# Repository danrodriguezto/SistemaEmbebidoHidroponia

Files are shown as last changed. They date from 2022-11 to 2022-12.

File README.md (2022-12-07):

# **Sistema Embebido para control de cultivo por hidroponia.** #

----
#### Daniel Esteban Rodriguez ####

#### Daniel Santiago Robayo ####

#### María Camila Muñoz Berrio ####

#### Sebastian Ruiz Torres ####

----
## **Descripción del problema** ## 

En la actualidad obtener alimentos vegetales con los nutrientes necesario y sin tanto procesamiento quimico a un valor moderado no es sencillo por lo que la idea de cultivar autonomamente los alimentos en una huerta casera se hace una mejor opción. Ahora, cultivar en la ciudad trae multiples desafios como los son el espacio, el tiempo que es posible dedicarle a esta labor y la falta de conocimiento en esto. De alli nacen vaias alternativas que pretenden reeemplazar las huertas en suelo convencionales por formas más eficientes de cutivar en el mismo espacio y por un valor menor.

Las principales alternativas son: Acuaponía, aeroponía e hidroponía. Esta ultima fue la elegida para desarrollar el proyecto debido a que esta se desarrolla en el agua, esto quiere decir que la raíz se desarrolla en un sustrato o en la misma solución liquida nutritiva utilizada.

## **Propuesta** ##
Se plantea construir un cultivo vertical de hidroponia que reduzca el espacio utilizado para un cultivo y que cuente con un sistema de monitoreo que cuente con sensores previamente calibrados que midan variables importantes para el sostenimiento del cultivo, estos sensores enviaran información que sera procesada y a partir de esto se enviaran alertas al telefono movil del usuario haciendo así interactivo el proceso de producir su alimento. También se pretende que esta dispositivo pueda ser usado por cualquier persona incluso si no conoce sobre hidroponia por medio de avisos informativos-educativos. 

**Publico objetivo** Personas con interesadas en cultivar en espacios reducidos sin la necesidad de dañar los suelos y aprender sobre cultivos hidroponicos.

**Objetivo General**  Diseño, creacion y aplicacion  de un sistema de monitoreo que permita la optimizacion del cultivo y la interaccion educativa con el usuario.

unknown

----
## **Requerimientos** ##
* Medir la temperatura de agua
* Medir el nivel del agua
* Ser ergonomico
* Recirculamiento del agua eficiente

## **Diagrama de bloques del sistema.** ##

En el siguiente diagrama se muestran los diferentes componentes que se plantean implementar en el sistema, en este se pueden observar cada una de las entradas y salidas que se pretenden tener en el sistema. Como interacción principal con el usuario se va a construir un sistema que conecte con el telefono del usuario y lo alerte sobre las condiciones de la planta.

Diagrama_en_blanco

## **Diagrama de caja negra con los modulos del ESP32.** ##
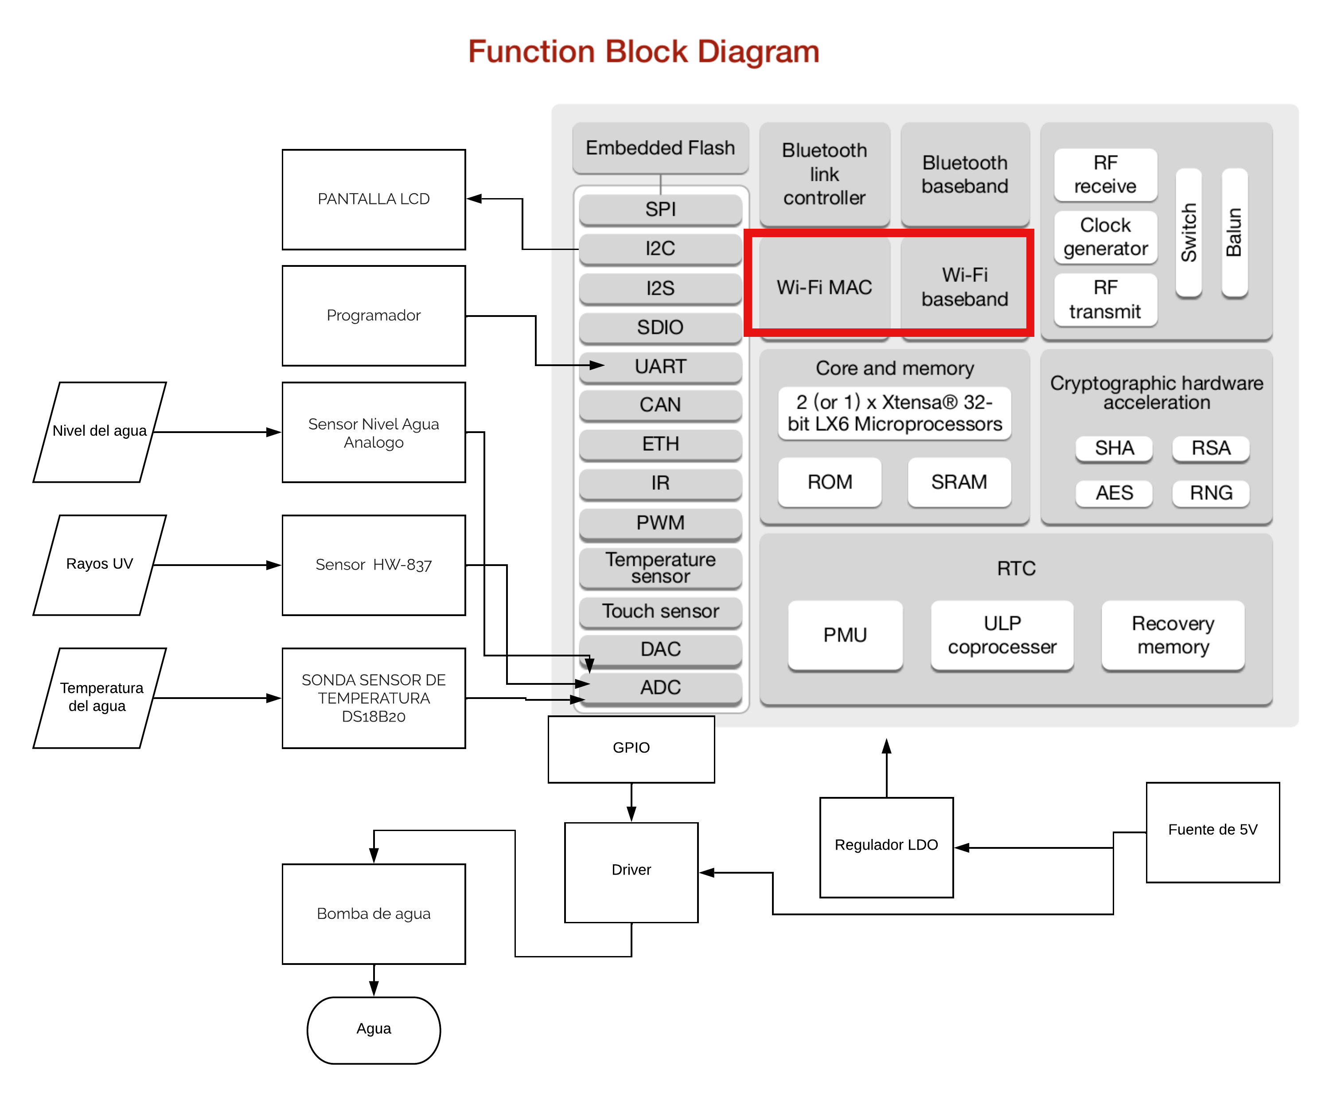
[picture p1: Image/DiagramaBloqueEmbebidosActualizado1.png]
Diagrama Bloque Embebidos


## **Diseño de la placa** ##

El diseño de la PCB fue hecho en el programa KiCad y se presentan los esquematicos a continuación,

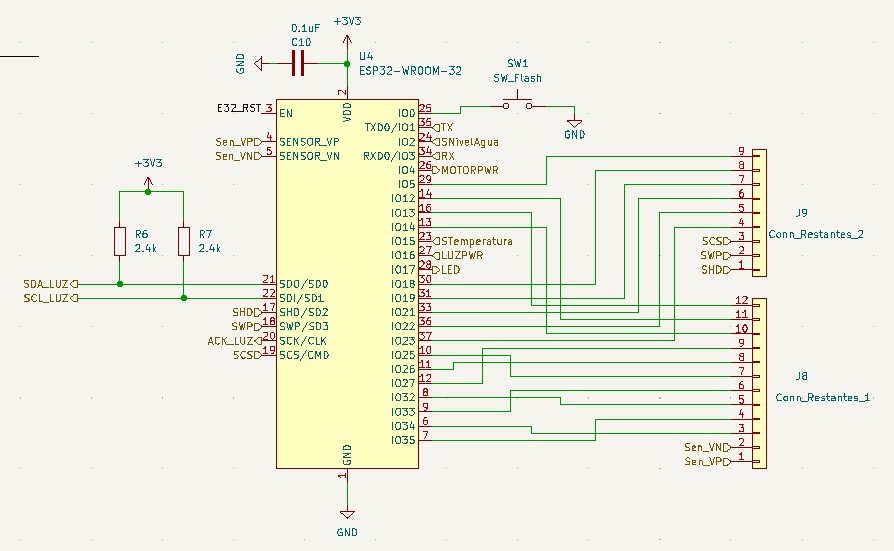
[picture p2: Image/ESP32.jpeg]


Se puede observar la distribución de los pines en el ESP32, la conexión de los sensores y la alimentación para este. Aqui se puede observar la conexión del interruptor de flash para subir el programa. 

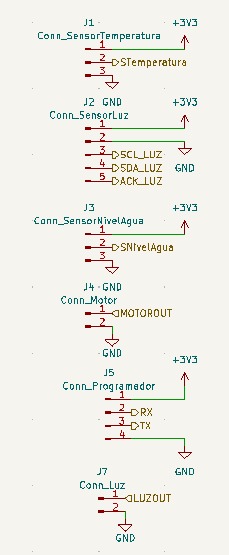
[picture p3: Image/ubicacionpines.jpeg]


Se puede detallar la distribución de los pines para cada sensor, con la respectiva alimentación y tierra.

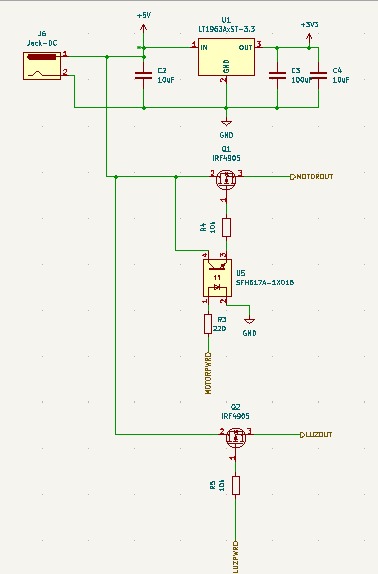
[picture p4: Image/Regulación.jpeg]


Aquí se presenta la configuración de la alimentación, el regulador(LT1963a5T-3.3), el octoacoplador(SFH617A-1Z01B) y los Mosfet utilizados (IRF4905).

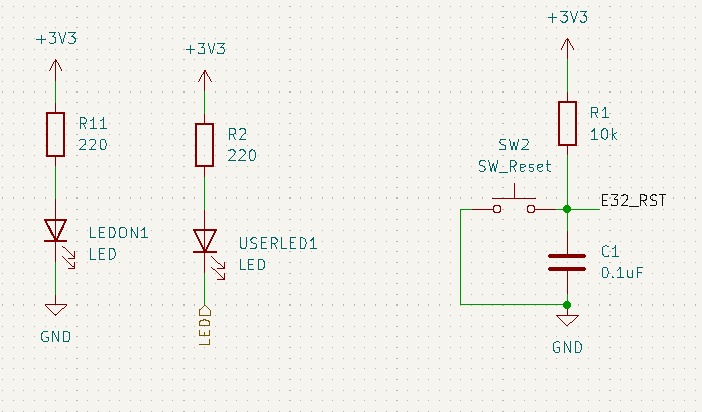
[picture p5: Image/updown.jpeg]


Esta fue la configuración para los led's utilizados, uno de iniciación y otro de boot. También se encuentran el  interruptor de reset.

De la misma manera se crea el diseño de la PCB de dos caras con medidas de 10cm X 10cm.

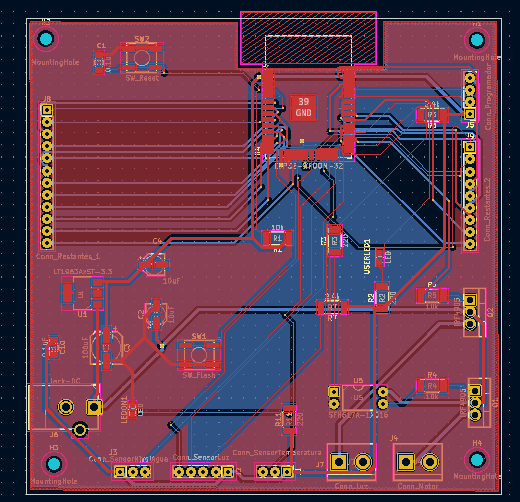
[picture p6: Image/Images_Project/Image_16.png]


Y a continuación se presentan ambas caras de la PCB.
Teniendo la cara frontal:

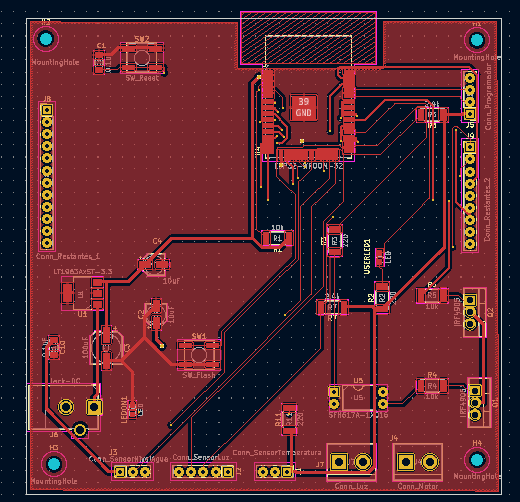
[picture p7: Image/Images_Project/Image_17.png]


Y la cara trasera:

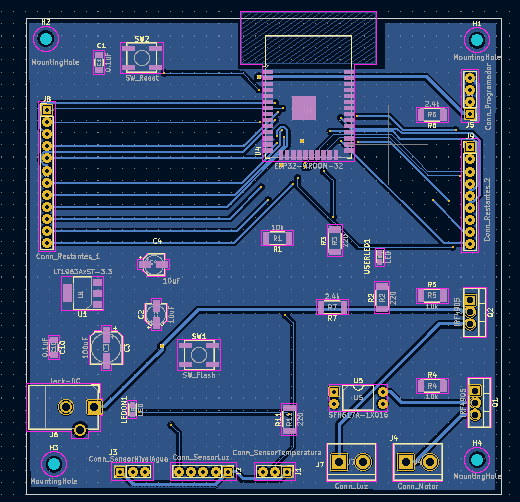
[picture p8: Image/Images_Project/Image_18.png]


Por lo tanto las imagenes de la PCB con sus componentes en 3D.

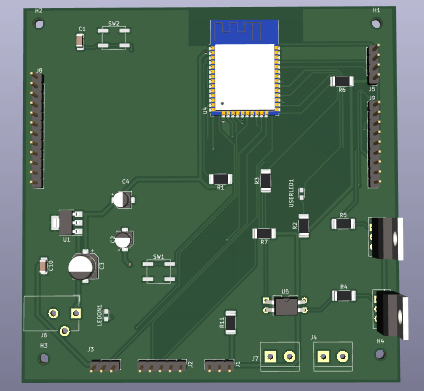
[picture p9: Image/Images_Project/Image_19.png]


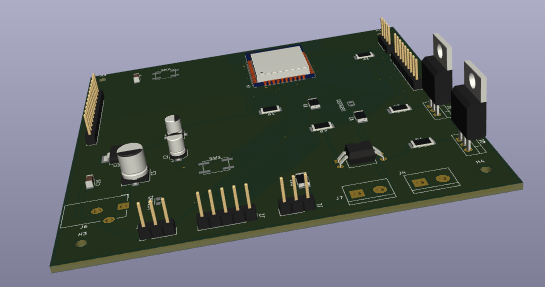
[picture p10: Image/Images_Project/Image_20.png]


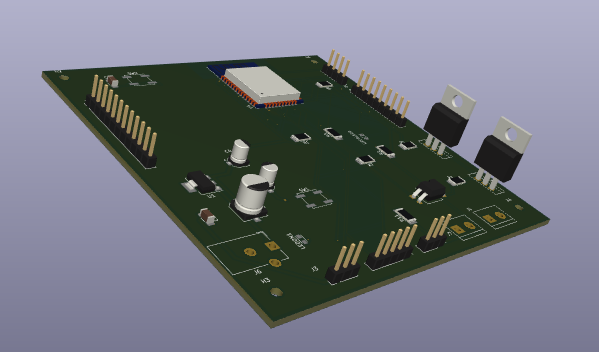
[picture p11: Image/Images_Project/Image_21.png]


## **Ensamble** ##

En primera instancia se recibio la PCB, fabricada en JLCPCB Hong Kong.

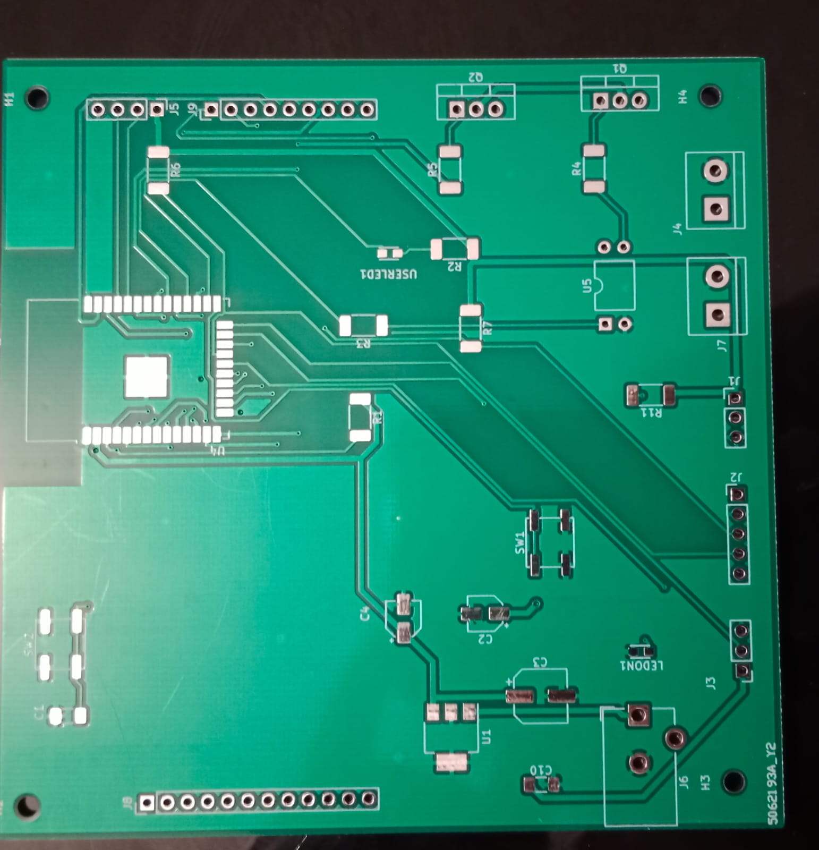
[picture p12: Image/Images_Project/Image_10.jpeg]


Luego se procede a conseguir los materiales para ser ensamblados en la PCB.

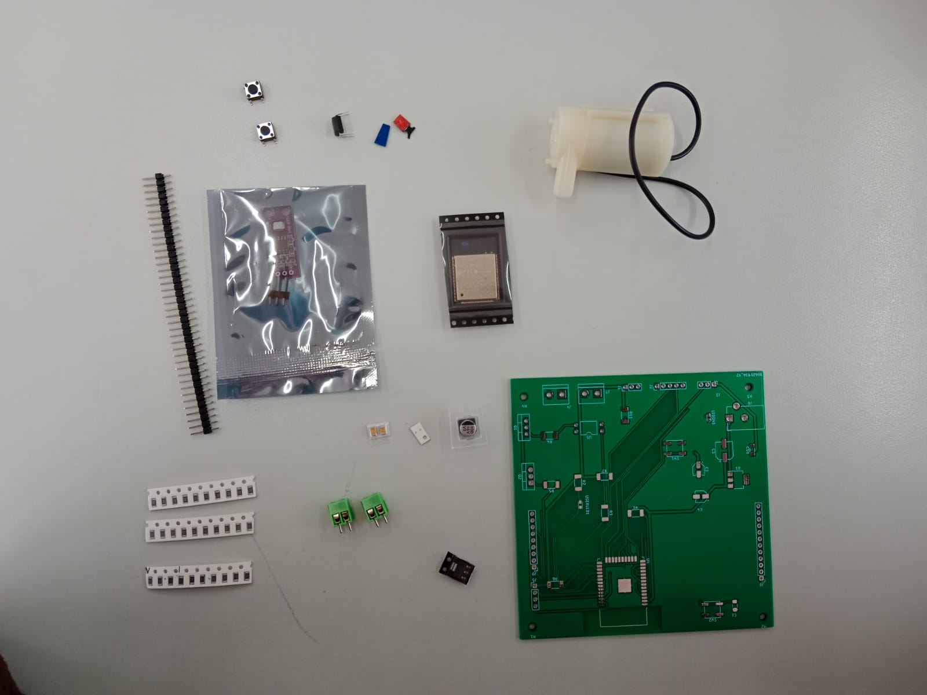
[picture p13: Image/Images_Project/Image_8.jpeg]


Y ya luego en el laboratorio de mecatronica se procedio a ensamblar todos los componentes.

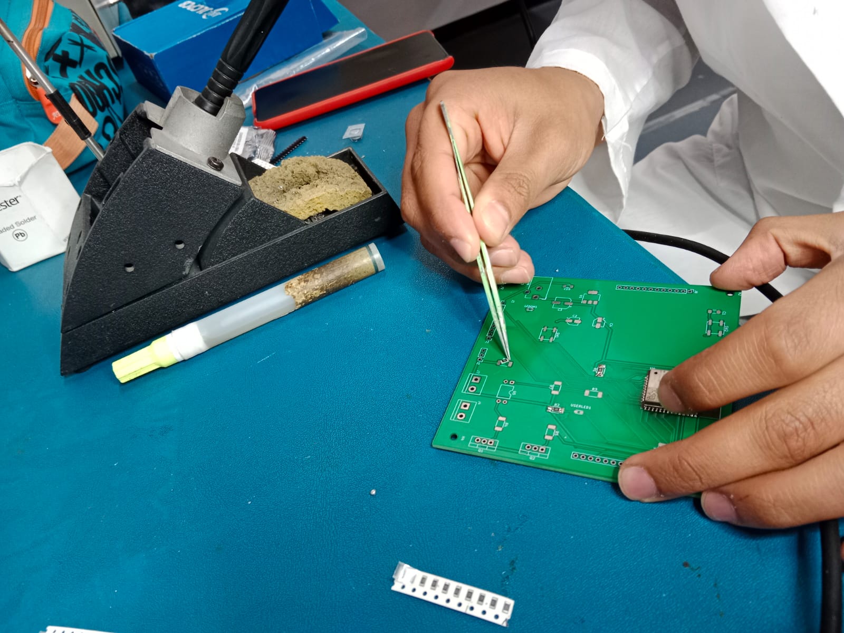
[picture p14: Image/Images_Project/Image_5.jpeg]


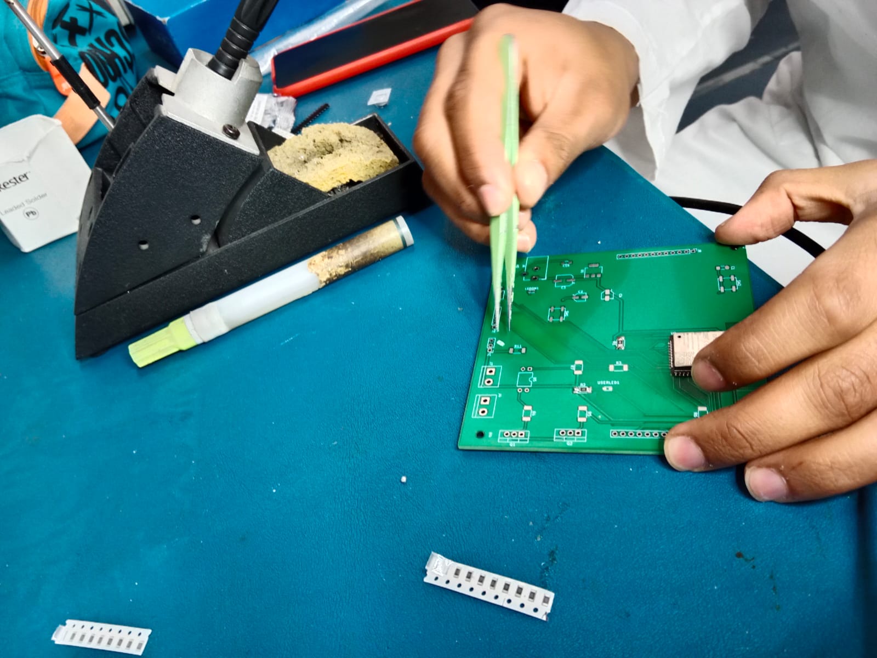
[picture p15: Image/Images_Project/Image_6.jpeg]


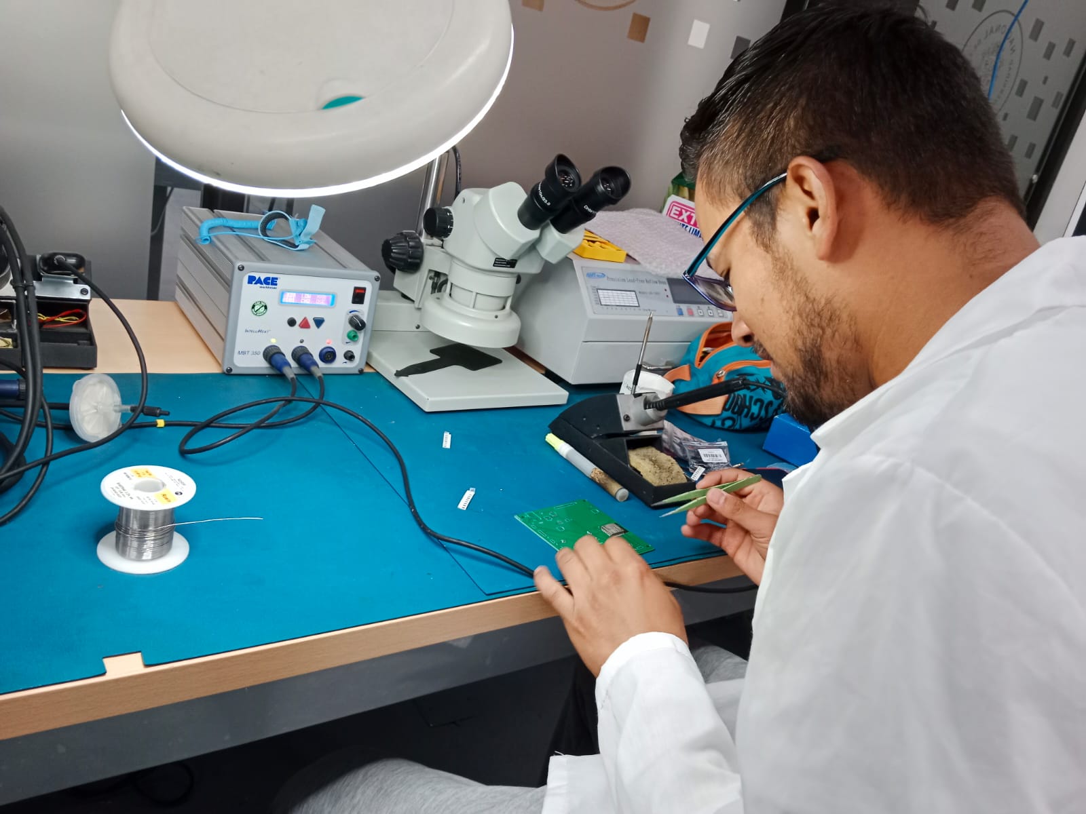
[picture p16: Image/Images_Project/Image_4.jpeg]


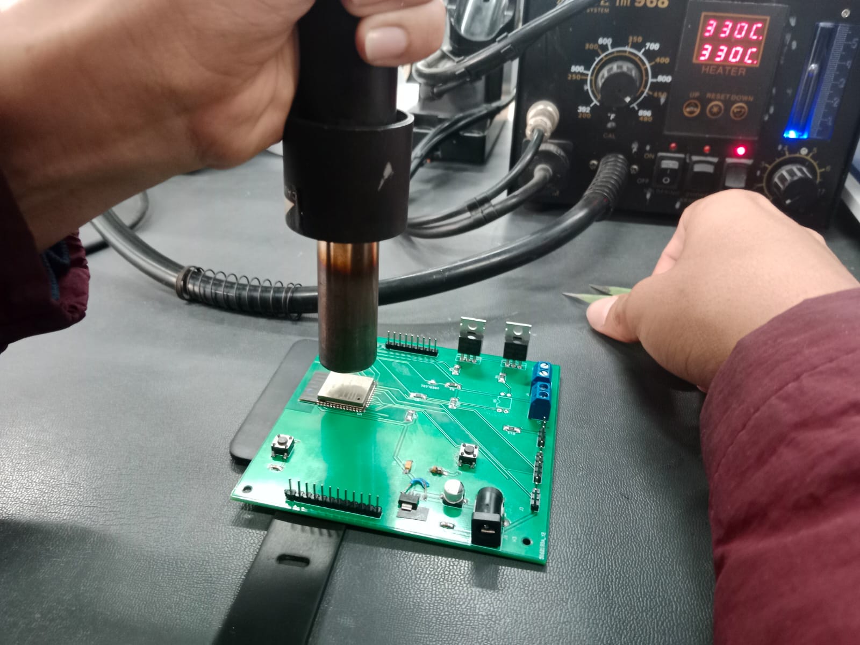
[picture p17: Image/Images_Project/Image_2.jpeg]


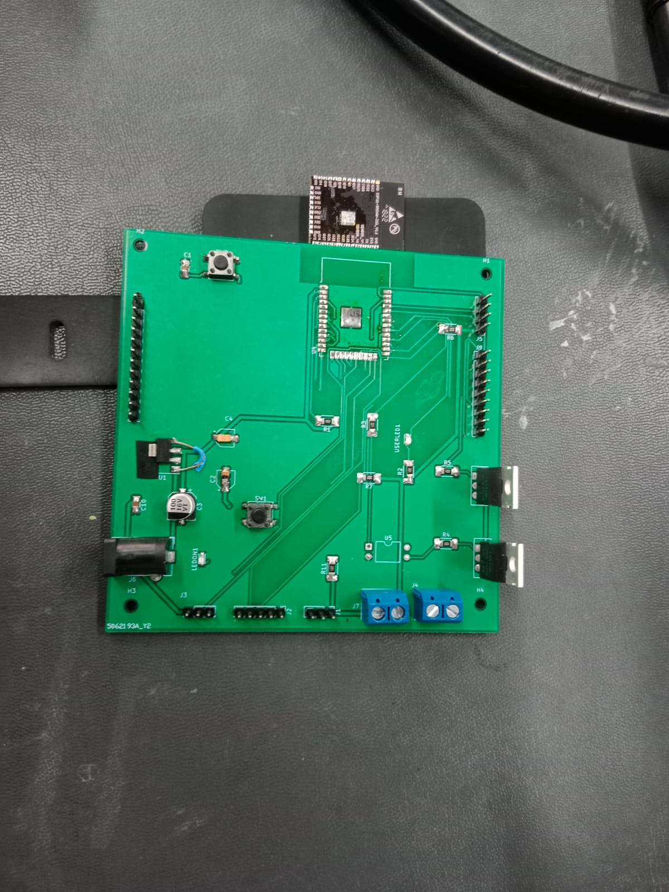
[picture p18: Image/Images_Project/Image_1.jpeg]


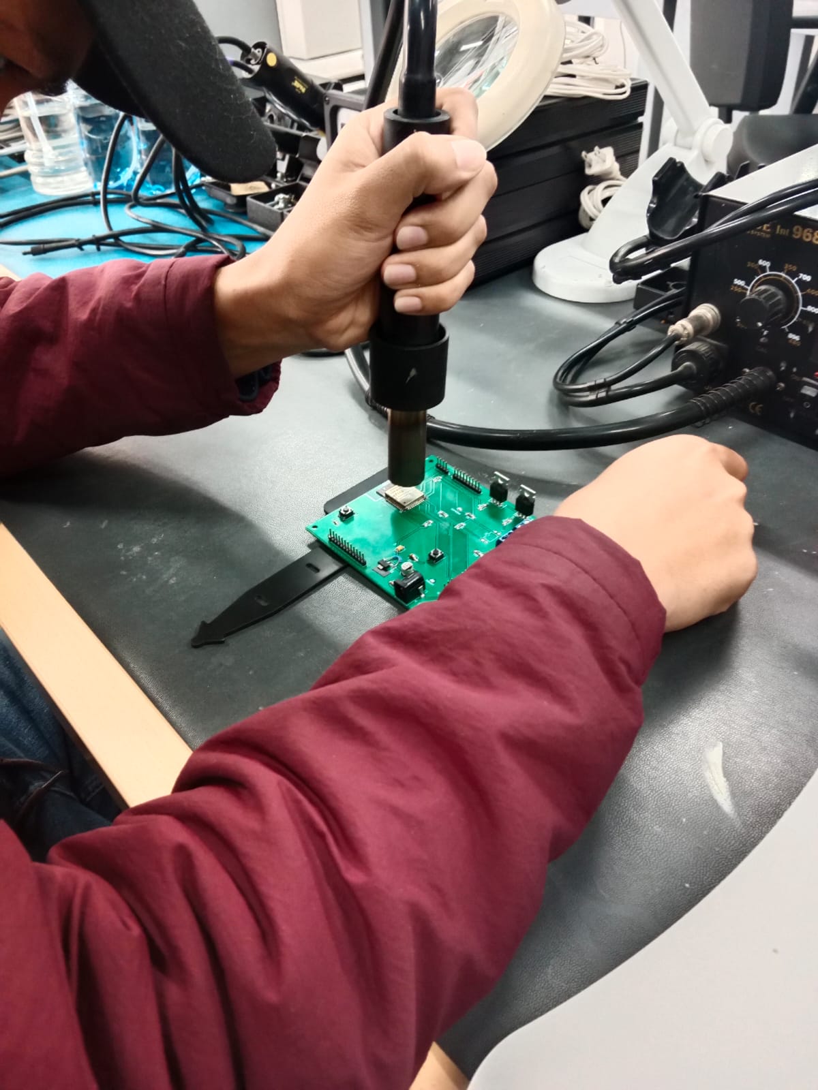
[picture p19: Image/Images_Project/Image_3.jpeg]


## **Resultados** ##

Este esquematico se puede ver en la placa ya con los sensores en la siguiente imágen.

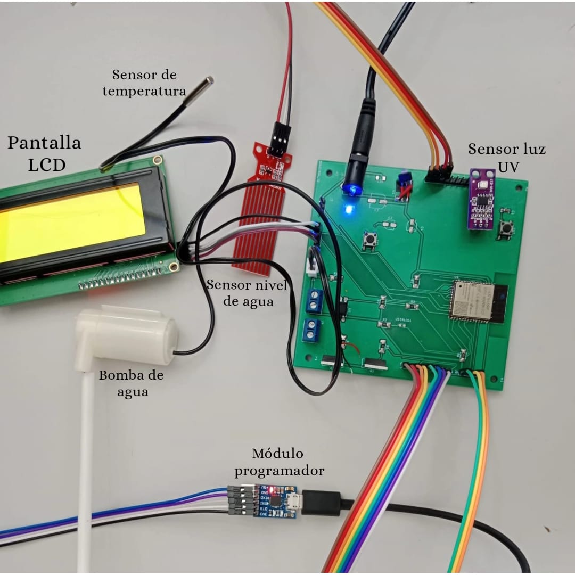
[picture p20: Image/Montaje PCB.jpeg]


Y el cultivo hidroponico.

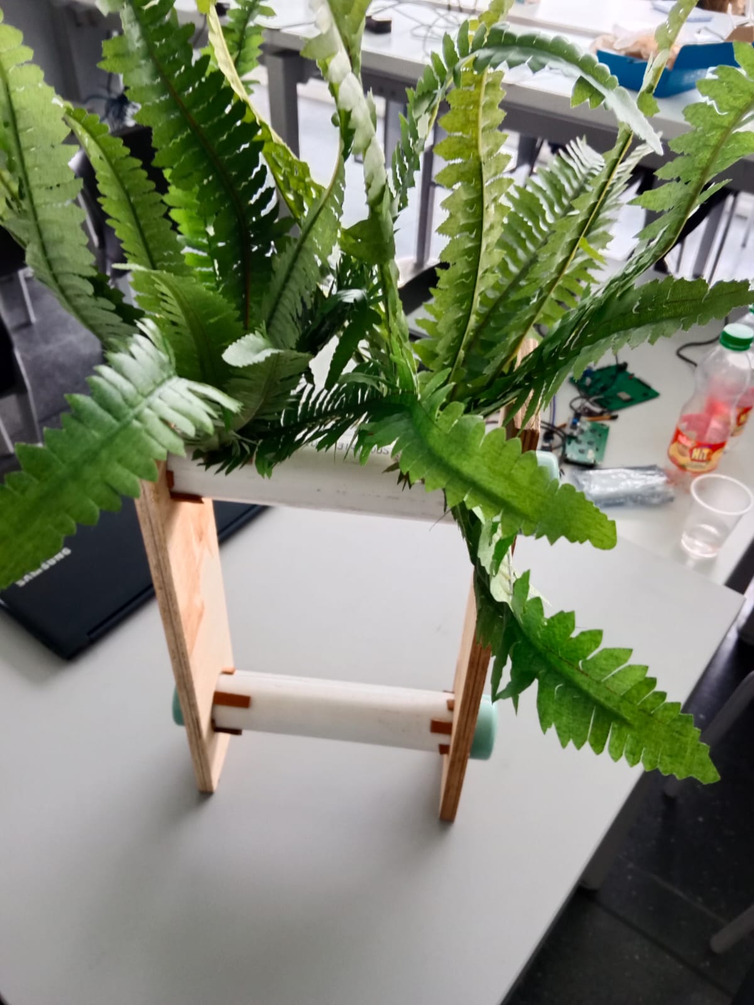
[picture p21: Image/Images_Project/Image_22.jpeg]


Y como producto final se tiene:

## **Brochure** ##

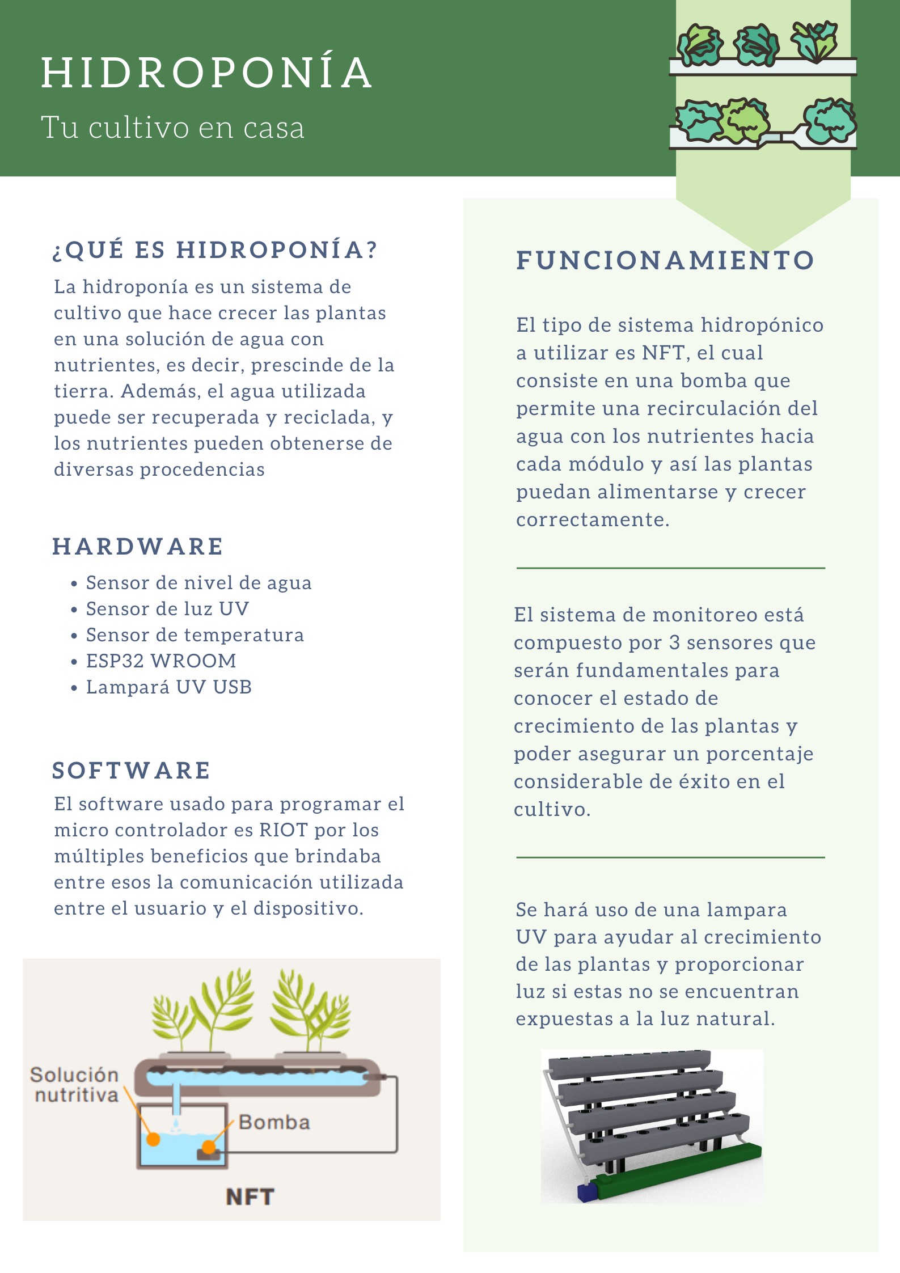
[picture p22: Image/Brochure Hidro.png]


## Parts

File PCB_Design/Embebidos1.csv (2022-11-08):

Source: | /home/danielrobayo/Documentos/GitHub/SistemaEmbebidoHidroponia/PCB_Design/Embebidos1.kicad_sch
Date: | mar 08 nov 2022 08:23:49
Tool: | Eeschema 6.0.9-8da3e8f707~116~ubuntu22.04.1
Generator: | /usr/share/kicad/plugins/bom_csv_grouped_by_value.py
Component Count: | 36
Individual Components:
Item | Qty | Reference(s) | Value | LibPart | Footprint | Datasheet
 |  | C1 | 0.1uF | Device:C | Capacitor_SMD:C_1206_3216Metric_Pad1.33x1.80mm_HandSolder | ~
 |  | C2 | 10uF | Device:C | Capacitor_SMD:CP_Elec_4x5.4 | ~
 |  | C3 | 100uF | Device:C | Capacitor_SMD:CP_Elec_6.3x7.7 | ~
 |  | C4 | 10uF | Device:C | Capacitor_SMD:CP_Elec_4x5.4 | ~
 |  | C10 | 0.1uF | Device:C | Capacitor_SMD:C_1206_3216Metric_Pad1.33x1.80mm_HandSolder | ~
 |  | H1 | MountingHole | Mechanical:MountingHole | MountingHole:MountingHole_2.5mm | ~
 |  | H2 | MountingHole | Mechanical:MountingHole | MountingHole:MountingHole_2.5mm | ~
 |  | H3 | MountingHole | Mechanical:MountingHole | MountingHole:MountingHole_2.5mm | ~
 |  | H4 | MountingHole | Mechanical:MountingHole | MountingHole:MountingHole_2.5mm | ~
 |  | H5 | MountingHole | Mechanical:MountingHole | MountingHole:MountingHole_2.5mm | ~
 |  | J1 | Conn_SensorTemperatura | Connector:Conn_01x03_Male | Connector_PinHeader_2.54mm:PinHeader_1x03_P2.54mm_Vertical | ~
 |  | J2 | Conn_SensorLuz | Connector:Conn_01x05_Male | Connector_PinHeader_2.54mm:PinHeader_1x05_P2.54mm_Vertical | ~
 |  | J3 | Conn_SensorNivelAgua | Connector:Conn_01x03_Male | Connector_PinHeader_2.54mm:PinHeader_1x03_P2.54mm_Vertical | ~
 |  | J4 | Conn_Motor | Connector:Conn_01x02_Male | Borneras:TerminalBlock_bornier-2_P5.08mm | ~
 |  | J5 | Conn_Programador | Connector:Conn_01x04_Male | Connector_PinHeader_2.54mm:PinHeader_1x04_P2.54mm_Vertical | ~
 |  | J6 | Jack-DC | Connector:Jack-DC | Connector_BarrelJack:BarrelJack_CUI_PJ-102AH_Horizontal | ~
 |  | J7 | Conn_Luz | Connector:Conn_01x02_Male | Borneras:TerminalBlock_bornier-2_P5.08mm | ~
 |  | J8 | Conn_Restantes_1 | Connector_Generic:Conn_01x12 | Connector_PinHeader_2.54mm:PinHeader_1x12_P2.54mm_Vertical | ~
 |  | J9 | Conn_Restantes_2 | Connector_Generic:Conn_01x09 | Connector_PinHeader_2.54mm:PinHeader_1x09_P2.54mm_Vertical | ~
 |  | LEDON1 | LED | Device:LED | LED_SMD:LED_miniPLCC_2315_Handsoldering | ~
 |  | Q1 | IRF4905 | Transistor_FET:IRF4905 | Package_TO_SOT_THT:TO-220-3_Vertical | http://www.infineon.com/dgdl/irf4905.pdf?fileId=5546d462533600a4015355e32165197c
 |  | Q2 | IRF4905 | Transistor_FET:IRF4905 | Package_TO_SOT_THT:TO-220-3_Vertical | http://www.infineon.com/dgdl/irf4905.pdf?fileId=5546d462533600a4015355e32165197c
 |  | R1 | 10k | Device:R | Resistor_SMD:R_2010_5025Metric_Pad1.40x2.65mm_HandSolder | ~
 |  | R2 | 220 | Device:R | Resistor_SMD:R_2010_5025Metric_Pad1.40x2.65mm_HandSolder | ~
 |  | R3 | 220 | Device:R | Resistor_SMD:R_2010_5025Metric_Pad1.40x2.65mm_HandSolder | ~
 |  | R4 | 10k | Device:R | Resistor_SMD:R_2010_5025Metric_Pad1.40x2.65mm_HandSolder | ~
 |  | R5 | 10k | Device:R | Resistor_SMD:R_2010_5025Metric_Pad1.40x2.65mm_HandSolder | ~
 |  | R6 | 2.4k | Device:R | Resistor_SMD:R_2010_5025Metric_Pad1.40x2.65mm_HandSolder | ~
 |  | R7 | 2.4k | Device:R | Resistor_SMD:R_2010_5025Metric_Pad1.40x2.65mm_HandSolder | ~
 |  | R11 | 220 | Device:R | Resistor_SMD:R_2010_5025Metric_Pad1.40x2.65mm_HandSolder | ~
 |  | SW1 | SW_Flash | Switch:SW_Push | Button_Switch_SMD:SW_SPST_EVPBF | ~
 |  | SW2 | SW_Reset | Switch:SW_Push | Button_Switch_SMD:SW_SPST_EVPBF | ~
 |  | U1 | LT1963AxST-3.3 | Regulator_Linear:LT1963AxST-3.3 | Package_TO_SOT_SMD:SOT-223-3_TabPin2 | https://www.analog.com/media/en/technical-documentation/data-sheets/1963aff.pdf
 |  | U4 | ESP32-WROOM-32 | RF_Module:ESP32-WROOM-32 | RF_Module:ESP32-WROOM-32 | https://www.espressif.com/sites/default/files/documentation/esp32-wroom-32_datasheet_en.pdf
 |  | U5 | SFH617A-1X016 | Isolator:SFH617A-1X016 | Package_DIP:DIP-4_W10.16mm | http://www.vishay.com/docs/83740/sfh617a.pdf
 |  | USERLED1 | LED | Device:LED | LED_SMD:LED_miniPLCC_2315_Handsoldering | ~
Collated Components:
Item | Qty | Reference(s) | Value | LibPart | Footprint | Datasheet
1 | 2 | C1, C10 | 0.1uF | Device:C | Capacitor_SMD:C_1206_3216Metric_Pad1.33x1.80mm_HandSolder | ~
2 | 2 | C2, C4 | 10uF | Device:C | Capacitor_SMD:CP_Elec_4x5.4 | ~
3 | 1 | C3 | 100uF | Device:C | Capacitor_SMD:CP_Elec_6.3x7.7 | ~
4 | 5 | H1, H2, H3, H4, H5 | MountingHole | Mechanical:MountingHole | MountingHole:MountingHole_2.5mm | ~
5 | 1 | J1 | Conn_SensorTemperatura | Connector:Conn_01x03_Male | Connector_PinHeader_2.54mm:PinHeader_1x03_P2.54mm_Vertical | ~
6 | 1 | J2 | Conn_SensorLuz | Connector:Conn_01x05_Male | Connector_PinHeader_2.54mm:PinHeader_1x05_P2.54mm_Vertical | ~
7 | 1 | J3 | Conn_SensorNivelAgua | Connector:Conn_01x03_Male | Connector_PinHeader_2.54mm:PinHeader_1x03_P2.54mm_Vertical | ~
8 | 1 | J4 | Conn_Motor | Connector:Conn_01x02_Male | Borneras:TerminalBlock_bornier-2_P5.08mm | ~
9 | 1 | J5 | Conn_Programador | Connector:Conn_01x04_Male | Connector_PinHeader_2.54mm:PinHeader_1x04_P2.54mm_Vertical | ~
10 | 1 | J6 | Jack-DC | Connector:Jack-DC | Connector_BarrelJack:BarrelJack_CUI_PJ-102AH_Horizontal | ~
11 | 1 | J7 | Conn_Luz | Connector:Conn_01x02_Male | Borneras:TerminalBlock_bornier-2_P5.08mm | ~
12 | 1 | J8 | Conn_Restantes_1 | Connector_Generic:Conn_01x12 | Connector_PinHeader_2.54mm:PinHeader_1x12_P2.54mm_Vertical | ~
13 | 1 | J9 | Conn_Restantes_2 | Connector_Generic:Conn_01x09 | Connector_PinHeader_2.54mm:PinHeader_1x09_P2.54mm_Vertical | ~
14 | 2 | LEDON1, USERLED1 | LED | Device:LED | LED_SMD:LED_miniPLCC_2315_Handsoldering | ~
15 | 2 | Q1, Q2 | IRF4905 | Transistor_FET:IRF4905 | Package_TO_SOT_THT:TO-220-3_Vertical | http://www.infineon.com/dgdl/irf4905.pdf?fileId=5546d462533600a4015355e32165197c
16 | 3 | R1, R4, R5 | 10k | Device:R | Resistor_SMD:R_2010_5025Metric_Pad1.40x2.65mm_HandSolder | ~
17 | 3 | R2, R3, R11 | 220 | Device:R | Resistor_SMD:R_2010_5025Metric_Pad1.40x2.65mm_HandSolder | ~
18 | 2 | R6, R7 | 2.4k | Device:R | Resistor_SMD:R_2010_5025Metric_Pad1.40x2.65mm_HandSolder | ~
19 | 1 | SW1 | SW_Flash | Switch:SW_Push | Button_Switch_SMD:SW_SPST_EVPBF | ~
20 | 1 | SW2 | SW_Reset | Switch:SW_Push | Button_Switch_SMD:SW_SPST_EVPBF | ~
21 | 1 | U1 | LT1963AxST-3.3 | Regulator_Linear:LT1963AxST-3.3 | Package_TO_SOT_SMD:SOT-223-3_TabPin2 | https://www.analog.com/media/en/technical-documentation/data-sheets/1963aff.pdf
22 | 1 | U4 | ESP32-WROOM-32 | RF_Module:ESP32-WROOM-32 | RF_Module:ESP32-WROOM-32 | https://www.espressif.com/sites/default/files/documentation/esp32-wroom-32_datasheet_en.pdf
23 | 1 | U5 | SFH617A-1X016 | Isolator:SFH617A-1X016 | Package_DIP:DIP-4_W10.16mm | http://www.vishay.com/docs/83740/sfh617a.pdf

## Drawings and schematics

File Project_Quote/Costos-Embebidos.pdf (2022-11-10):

# COSTOS EMBEBIDOS

SENSORES | ELEMENTOS PCB

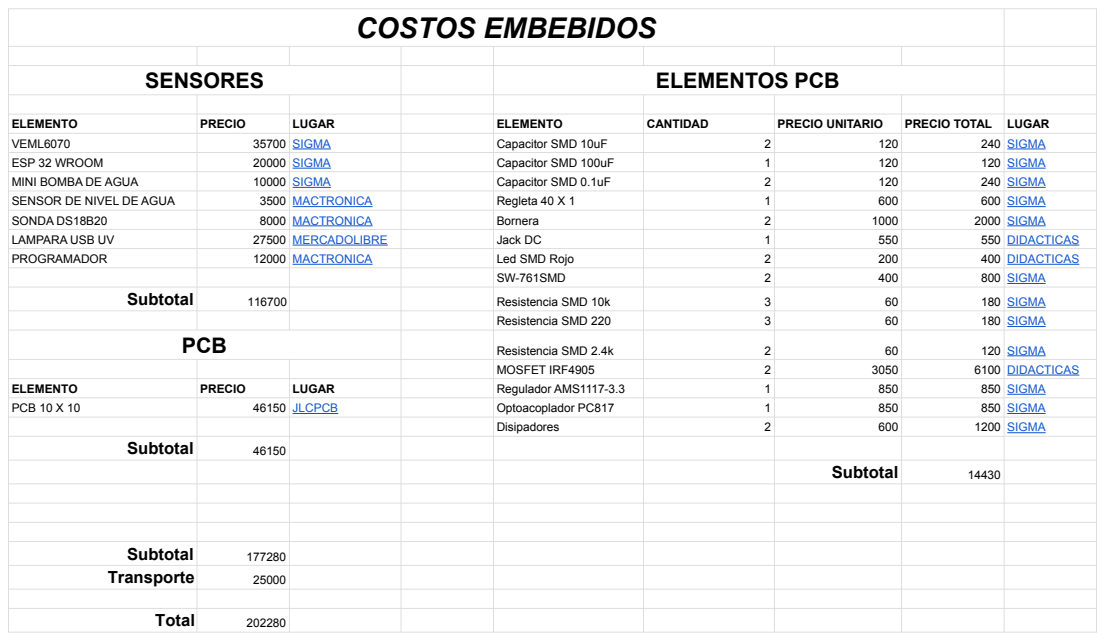
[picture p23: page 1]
ELEMENTO; PRECIO; LUGAR; CANTIDAD; PRECIO UNITARIO; PRECIO TOTAL; VEML6070; 35700 SIGMA; Capacitor SMD 10uF; 240 SIGMA; ESP 32 WROOM; 20000 SIGMA; Capacitor SMD 100uF; 120 SIGMA; MINI BOMBA DE AGUA; 10000 SIGMA; Capacitor SMD 0.1uF; SENSOR DE NIVEL DE AGUA; 3500 MACTRONICA; Regleta 40 X 1; 600 SIGMA; SONDA DS18B20; 8000 MACTRONICA; Bornera; 2000 SIGMA; LAMPARA USB UV; 27500 MERCADOLIBRE; Jack DC; 550 DIDACTICAS; PROGRAMADOR; 12000 MACTRONICA; Led SMD Rojo; 400 DIDACTICAS; SW-761SMD; 800 SIGMA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

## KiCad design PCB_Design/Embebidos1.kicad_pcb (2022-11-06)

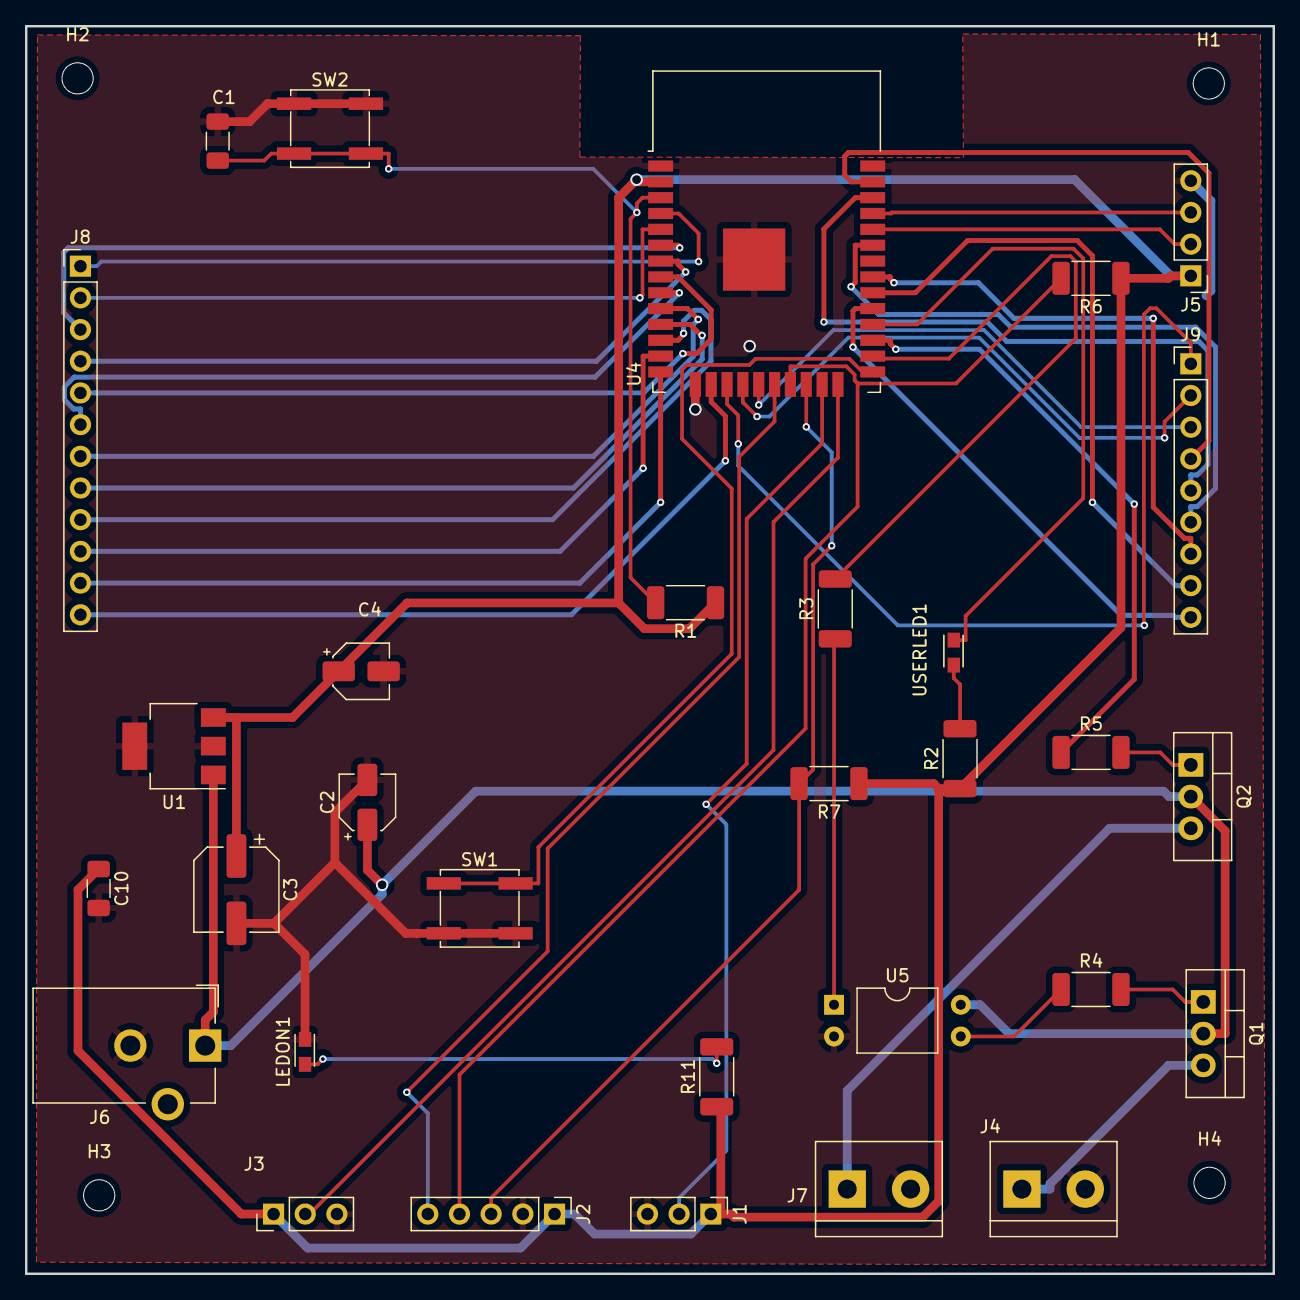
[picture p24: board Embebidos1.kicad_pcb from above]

Board: 2 copper layers, 100.0 x 100.0 mm, 35 parts (0 on the bottom side), 44 nets.

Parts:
C1, C10: 0.1uF; C_1206_3216Metric_Pad1.33x1.80mm_HandSolder
C2, C4: 10uF; CP_Elec_4x5.4
C3: 100uF; CP_Elec_6.3x7.7
H1, H2, H3, H4: MountingHole; MountingHole_2.5mm
J1: Conn_SensorTemperatura; PinHeader_1x03_P2.54mm_Vertical
J2: Conn_SensorLuz; PinHeader_1x05_P2.54mm_Vertical
J3: Conn_SensorNivelAgua; PinHeader_1x03_P2.54mm_Vertical
J4: Conn_Motor; TerminalBlock_bornier-2_P5.08mm
J5: Conn_Programador; PinHeader_1x04_P2.54mm_Vertical
J6: Jack-DC; BarrelJack_CUI_PJ-102AH_Horizontal
J7: Conn_Luz; TerminalBlock_bornier-2_P5.08mm
J8: Conn_Restantes_1; PinHeader_1x12_P2.54mm_Vertical
J9: Conn_Restantes_2; PinHeader_1x09_P2.54mm_Vertical
LEDON1: LED; LED_miniPLCC_2315_Handsoldering
Q1, Q2: IRF4905; TO-220-3_Vertical
R1, R4, R5: 10k; R_2010_5025Metric_Pad1.40x2.65mm_HandSolder
R2, R3, R11: 220; R_2010_5025Metric_Pad1.40x2.65mm_HandSolder
R6, R7: 2.4k; R_2010_5025Metric_Pad1.40x2.65mm_HandSolder
SW1: SW_Flash; SW_SPST_EVPBF
SW2: SW_Reset; SW_SPST_EVPBF
U1: LT1963AxST-3.3; SOT-223-3_TabPin2
U4: ESP32-WROOM-32
U5: SFH617A-1X016; DIP-4_W10.16mm
USERLED1: LED; LED_miniPLCC_2315_Handsoldering

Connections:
+3V3: C3.1, C4.1, C10.1, J1.1, J2.1, J3.1, J5.1, R1.1, R2.1, R6.1, R7.1, R11.1, U1.3 (OUT), U4.2 (VDD)
+5V: C2.1, J6.1, Q1.2 (D), Q2.2 (D), U1.1 (IN), U5.4
/ACK_LUZ: J2.5, U4.20 (SCK/CLK)
/E32_RST: C1.1, R1.2, SW2.2, U4.3 (EN)
/LED: U4.28 (IO17), USERLED1.1 (K)
/LUZOUT: J7.1, Q2.3 (S)
/LUZPWR: R5.1, U4.27 (IO16)
/MOTOROUT: J4.1, Q1.3 (S)
/MOTORPWR: R3.2, U4.26 (IO4)
/RX: J5.2, U4.34 (RXD0/IO3)
/SCL_LUZ: J2.3, R7.2, U4.22 (SDI/SD1)
/SCS: J9.3, U4.19 (SCS/CMD)
/SDA_LUZ: J2.4, R6.2, U4.21 (SDO/SD0)
/SHD: J9.1, U4.17 (SHD/SD2)
/SNivelAgua: J3.2, U4.24 (IO2)
/STemperatura: J1.2, U4.23 (IO15)
/SWP: J9.2, U4.18 (SWP/SD3)
/Sen_VN: J8.2, U4.5 (SENSOR_VN)
/Sen_VP: J8.1, U4.4 (SENSOR_VP)
/TX: J5.3, U4.35 (TXD0/IO1)
GND: C1.2, C2.2, C3.2, C4.2, C10.2, J1.3, J2.2, J3.3, J4.2, J5.4, J6.2, J7.2, LEDON1.1 (K), SW1.2, SW2.1, U1.2 (GND), U4.1 (GND), U4.15 (GND), U4.38 (GND), U4.39 (GND), U5.2
unnamed: LEDON1.2 (A), R11.2
unnamed: Q1.1 (G), R4.2
unnamed: Q2.1 (G), R5.2
unnamed: R2.2, USERLED1.2 (A)
unnamed: R3.1, U5.1
unnamed: R4.1, U5.3
unnamed: SW1.1, U4.25 (IO0)
unnamed: J8.3, U4.6 (IO34)
unnamed: J8.4, U4.7 (IO35)
unnamed: J8.5, U4.8 (IO32)
unnamed: J8.6, U4.9 (IO33)
unnamed: J8.7, U4.10 (IO25)
unnamed: J8.8, U4.11 (IO26)
unnamed: J8.9, U4.12 (IO27)
unnamed: J8.10, U4.13 (IO14)
unnamed: J8.11, U4.14 (IO12)
unnamed: J8.12, U4.16 (IO13)
unnamed: J9.9, U4.29 (IO5)
unnamed: J9.8, U4.30 (IO18)
unnamed: J9.7, U4.31 (IO19)
unnamed: J9.6, U4.33 (IO21)
unnamed: J9.5, U4.36 (IO22)
unnamed: J9.4, U4.37 (IO23)

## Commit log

2022-11-06 PCB
    PCB
    [Embebidos1-B_Cu.gbr, Embebidos1-B_Mask.gbr, Embebidos1-B_Paste.gbr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]
2022-11-08 Costos
    Costos
    [Embebidos1.csv]
2022-12-07 Create ESP32
